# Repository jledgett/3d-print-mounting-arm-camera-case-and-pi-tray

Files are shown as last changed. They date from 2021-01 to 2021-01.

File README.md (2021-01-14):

# 3D Printer: Mounting Arm and Case for Raspberry Pi HQ Camera and Raspberry Pi / OctoPi

## Overview

This collection of files will allow you to 3D print a modification to your 3D printer.  This modification adds a mounting arm, case for the Raspberry Pi HQ Camera, as well as a covered tray for a Raspberry Pi 4B.  This is particularly useful for adding a camera to your printer for monitoring and control using OctoPrint / OctoPi.

This system was designed to work with the Creality CR-6 SE printer, but should work with __any__ printer or CNC that uses a 40mm x 40mm extruded aluminum frame (including Ender 3, Ender 3 Pro, CR-10 MAX) .

The Raspberry Pi case for your OctoPi server is designed to allow either direct mounting of the Raspberry Pi to the case using standoffs or dropping in the popular aluminum Flirc case for better heat dissipation.   

The case also supports mounting a **5v** 40mm fan.   Noctua fans are suggested due to their quiet operation and lengthy warranty.   They also included the 3-pin to 2-pin adapter which will allow you connect it directly to pins 4 and 6 of your Raspberry Pi's GPIO.

If you are using the Flirc case, the camera cable and fan cable can both be passed through the GPIO slot on the bottom of the Flirc case.   Remove the cosmetic black plastic TOP panel to increase cooling performance.

## Getting Started

You will need the following non-included parts:
- [Raspberry Pi 4B](https://smile.amazon.com/gp/product/B08DJ9MLHV/)
- [Raspberry Pi HQ Camera](https://www.canakit.com/raspberry-pi-hq-camera.html)
- [SD Card](https://smile.amazon.com/gp/product/B07FCMKK5X)
- [6mm CS-mount Lens](https://smile.amazon.com/gp/product/B088GWZPL1)
- [Flex Cable for Raspberry Pi Camera or Display - 18" / 457mm](https://www.adafruit.com/product/1730)
- [Mini Ball Head](https://smile.amazon.com/gp/product/B01N7RYA87) NOTE: Alternatively, you can mount directly to the mounting arm but will lose the ability to adjust the pitch of the camera up and down.
- [Noctua 40mm 5V Fan (3-pin)](https://smile.amazon.com/gp/product/B00NEMGCIA) (includes 3-pin to 2-pin adapter)
- *Screws, Nuts, Bolts*
  - (2x) 1/4"-20 x 1/2" bolts
  - (1x) 1/4"-20 jam nut
  - (4x) M4 x 40mm machine screws
  - (4x) M4 nuts
  - (6x) M4 washers
  - (4x) M2.5 x 30mm (or M2.5 x 35mm) 
  - (8x) M2.5 nuts
  - (8x) M2.5 washers
  - (4x) M2.5 nylon/rubber isolating washers
- [Flirc Raspberry Pi 4 Case](https://www.amazon.com/Flirc-Raspberry-Pi-Case-Silver/dp/B07WG4DW52/) _**OR**_
   - (4x) M2.5 x 10mm stand offs with matching screws
   - (4x) M2.5 nuts
   - (4x) M2.5 nylon/rubber isolating washers

You will need the following additional tools:
- Screwdriver for M2.5 screws
- Screwdriver for M4 screws
- Needle-nose pliers
- 1/4"-20 tap and die set for cleaning up threads of leveling feet

## Printing Instructions

:warning: **IMPORTANT:** Please review each part in your slicing software before printing to ensure a logical face is touching the build plate!      

These print settings were used to print using a Creality CR-6 SE using Hatchbox Black 1.75mm PLA.   You may need to adjust these settings slightly for other printer and filament combinations.

- Print Resolution: 0.2
- Infill (unless otherwise noted below): 40%
- Supports (unless otherwise noted below): No
- Printing Temperature: 200C
- Build Plate Temperature: 60C
- Part-specific notes:
   - **Short Leveling Foot 1g - Print 5.stl**: Print 5 of these at 100% infill.
   - **Long Leveling Foot 1g - Print 2.stl**: Print 2 of these at 100% infill.
   - **Tripod Thread Mount 34g.stl**: This piece is optional.   Print it if you want to mount accessories such as an LED light.   For this piece you will need to print a "Touching Buildplate" support for overhanging angles exceeding 47°.  This is the only piece that needs to be printed with supports.
  - **OPTIONAL Octopi Tray Spring Clip For FLIRC Case 4g.stl**: This is only needed if you are dropping in a Flirc case.  It ensures the case stays aligned properly.

## Assembly Instructions

1. Clean up the threaded parts (both male and female) using a tap and die.   Silicone spray can assist with lubricating the threads before screwing them.

1. Attach the fan to the OctoPi Tray using the self-tapping mounting screws that came with the fan.

1. Use an M4 screw and nut to attach the Mounting Arm to the Mounting Arm Rail Clamp.

1. Use the three remaining M4 screws, washers, and nuts as well as the OctoPi Tray spacers to attach the Mounting Arm to the OctoPi Tray. 

1. Attach the five Short Leveling Feet to the appropriate holes on the bottom of the OctoPi tray and Mounting Arm.

1. Snap the Mounting Arm Rail Clamp to the left front of the 3d printer.   

1. Attach the Raspberry Pi camera cable to the Raspberry Pi.

1. Attach the fan cable adapter to pins 4 and 6 (pin 4 is 5v, pin 6 is ground) of the Raspberry Pi.  

1. If using a Flirc case, unclip the cosmetic black top panel and set aside.  Place the Pi inside the case and route the cables through the bottom GPIO slot.

1. Place the Raspberry Pi in the OctoPi tray and route the Raspberry Pi camera cable through the triangular opening of the tray.   Feed the cable up through the cable guiding slot in the mounting arm.

1. Attach the lens to the camera.

1. Feed the other end of the Raspberry Pi camera cable through the slot of the Camera Case back and attach it to the Raspberry Pi HQ Camera.  Ensure correct orientation.  

1. Place the four M2.5 x 30mm screws and washers through the rear of the Camera case back and the HQ camera.   Place a nylon/rubber M2.5 washer on each of the four screws.   Then place an M2.5 nut on each of the four screws, finger tightening to hold the camera in place.  

1. Attach the mini ball head to the Mounting Arm using 1/4"-20 x 1/2" bolt.

1. Screw the 1/4"-20 jam nut on the mini ball head.    

1. Carefully attach the Camera case back and HQ camera to the mini ball head using the HQ camera's integrated tripod thread.   Tighten the jam nut in place to secure the the camera.

1. Route the USB-C power source along the rail of your printer, tucking the cord into the top channel of the aluminum extrusion where possible.   Route the cable under the OctoPi Tray spacer closest to the printer.

1. Route the USB-C power source through the square hole in the OctoPi Tray Lid and plug it in to the Raspberry Pi.   

1. If using a Flirc case, place the spring clip in the side of the case closest to the USB and network ports.   This clip simply holds the Flirc case against the side of the case opposite the fan.

1. Drop the OctoPi Tray Lid in place.

1. Use the USB C cord retainers to clip the USB C power source into place on the rail.

1. [Install OctoPi on your Raspberry Pi](https://octoprint.org/download/) (the SD card is accessible through the slot on the end of the OctoPi Tray).

1. Once OctoPi is running, go the Control tab and you should see a web camera image.    

1. The camera may appear in 4:3 ratio instead of 16x9 regardless of the OctoPrint settings.   You can fix this by SSHing into your OctoPi and editing: `boot/octopi.txt`

1. Adjust the focus and apeture of your camera and tighten the adjustment thumbscrews in place.   

1. Slide the Camera Case Front carefully on to the four screws.   Using the M2.5 washers and nuts, carefully secure the case in place.

1. If you wish to use the Tripod Thread Mount, insert the 2 Long Leveling Feet to the mount.

1. Clamp the Tripod Thread Mount to the left rear of the 3d printer.   Your light, etc. can be attached to the mount using the remaining 1/4"-20 x 1/2" bolt.

1. Adjust all the leveling feet.

1. Plug in a voltage isolated **(NO 5V PIN!)** USB-A to Micro USB cable from the Raspberry Pi to the printer.  It is **very important** to ensure that your cable does not have a 5V pin or your printer  and Raspberry Pi may be damaged!

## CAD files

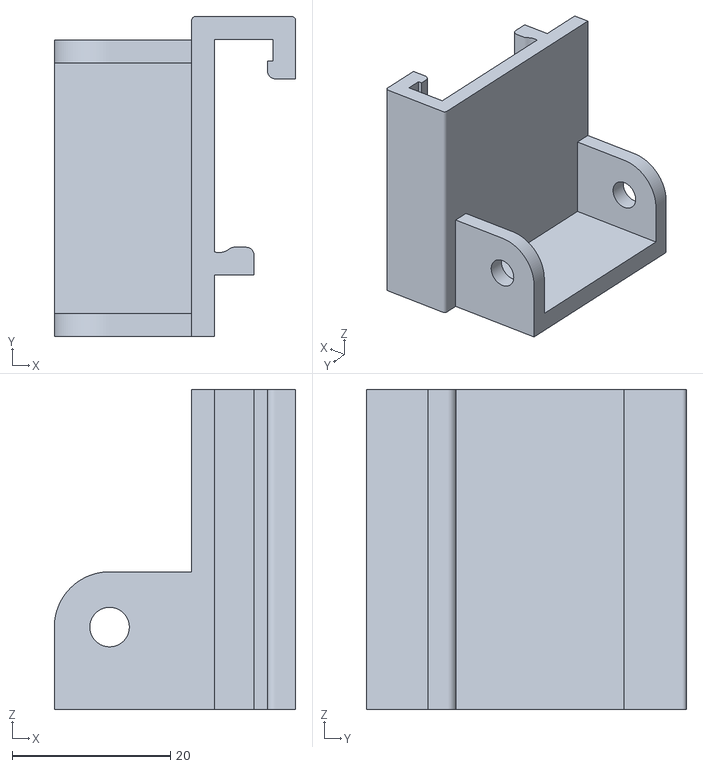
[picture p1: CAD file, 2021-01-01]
Mounting Arm Rail Clamp 10g.stl
30.6 x 40.5 x 40.5

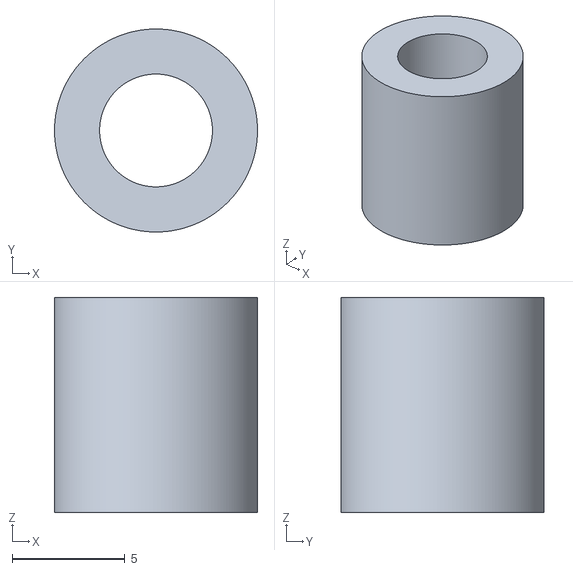
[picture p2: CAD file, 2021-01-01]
Octopi Tray Spacer 1g - Print 3.stl
9.00 x 9.00 x 9.55

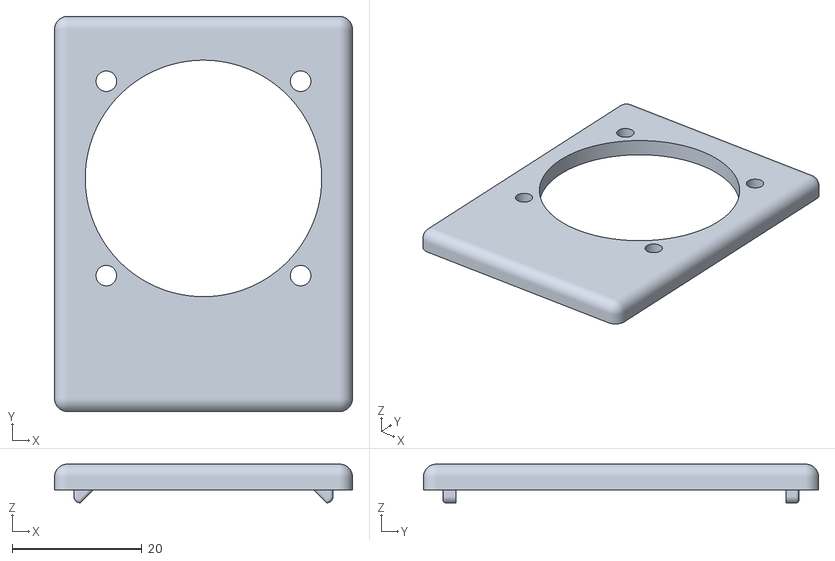
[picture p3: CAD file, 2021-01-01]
Camera Case Front 6g.stl
46.0 x 61.0 x 6.00

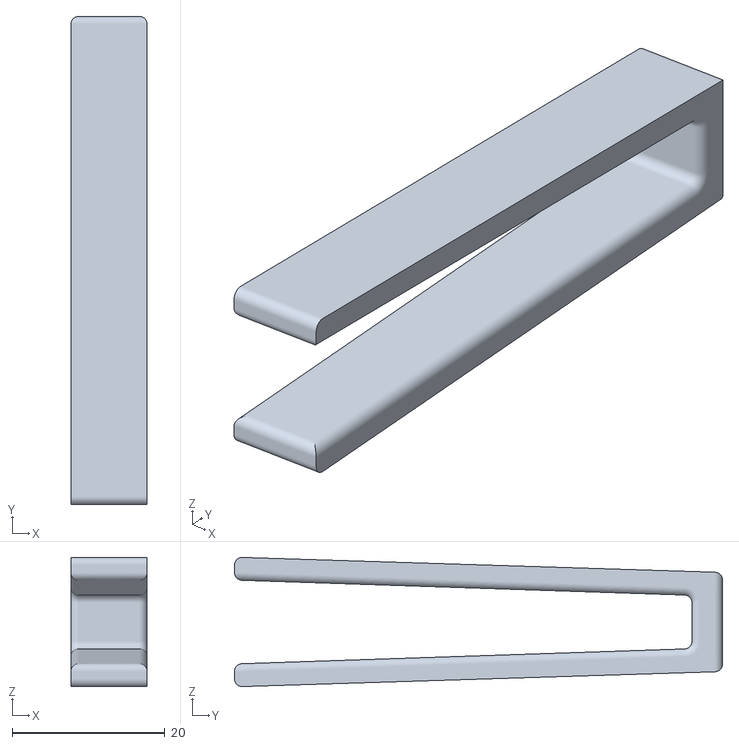
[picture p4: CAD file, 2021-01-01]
OPTIONAL Octopi Tray Spring Clip For FLIRC Case 4g.stl
10.0 x 64.0 x 16.9

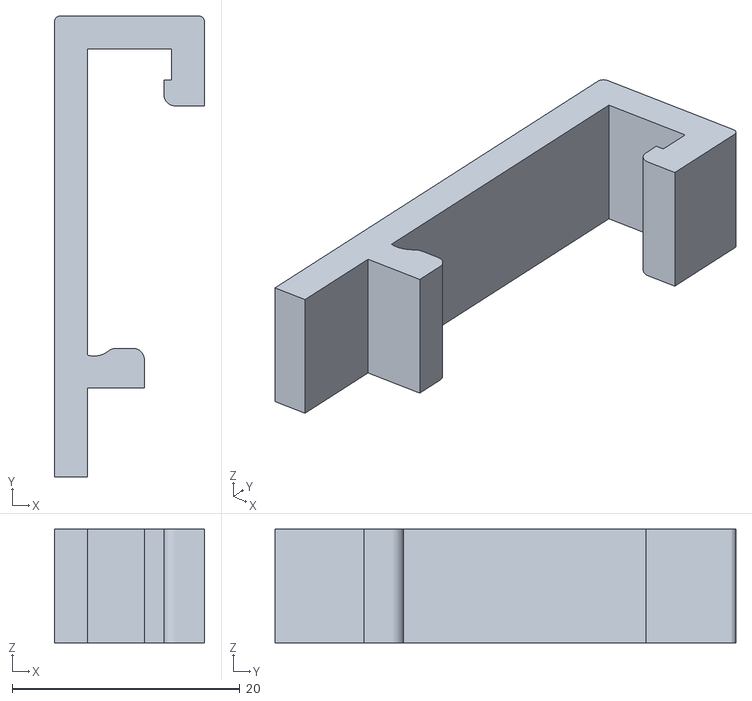
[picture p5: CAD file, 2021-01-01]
USB C Cord Retainer 2g - Print 2.stl
13.2 x 40.5 x 10.0

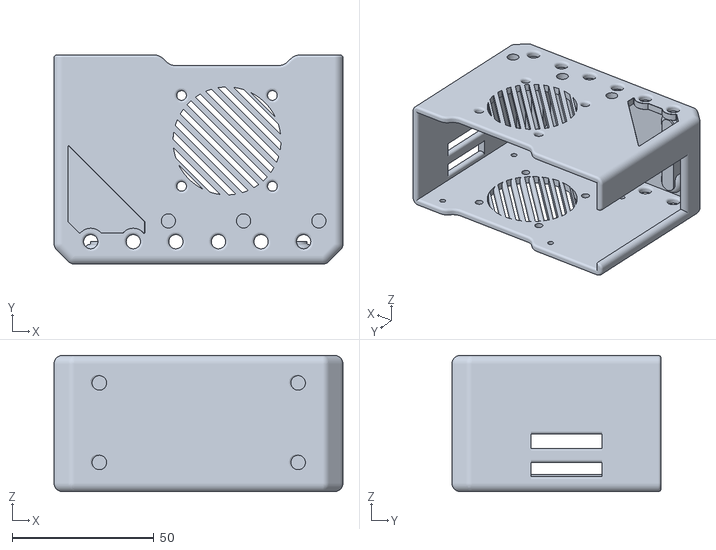
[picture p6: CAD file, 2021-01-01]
Octopi Tray 60g.stl
101.8 x 73.7 x 48.0

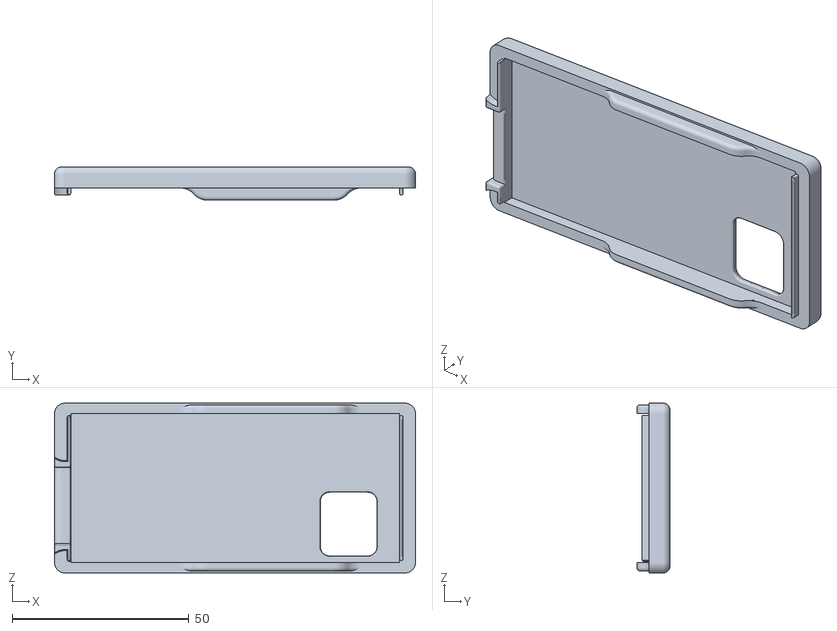
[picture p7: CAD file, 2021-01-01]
Octopi Tray Lid 16g.stl
102.0 x 9.41 x 48.0

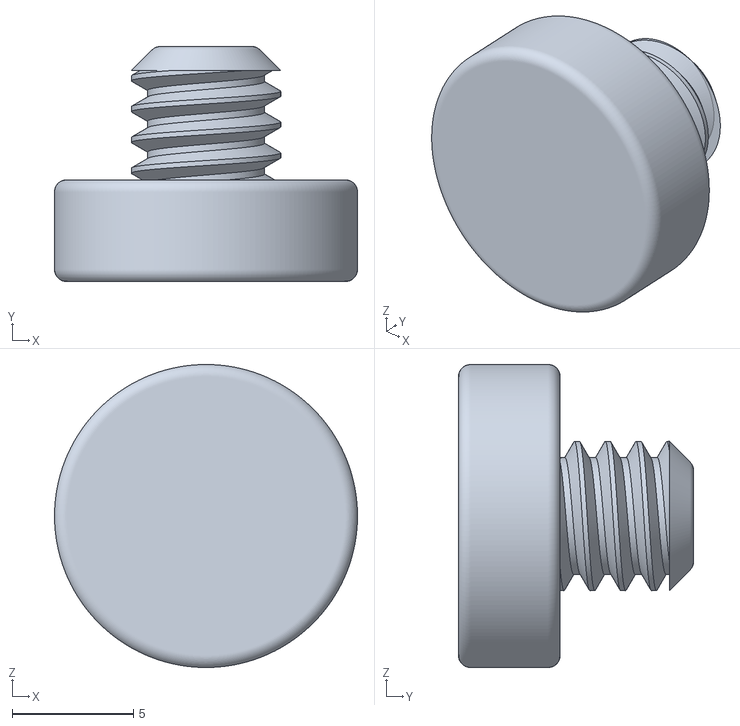
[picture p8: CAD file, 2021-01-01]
Short Leveling Foot 1g - Print 5.stl
12.5 x 9.70 x 12.5

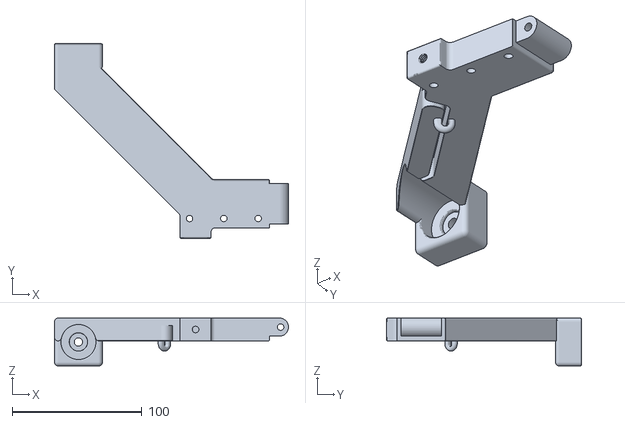
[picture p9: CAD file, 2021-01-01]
Mounting Arm 92g.stl
180.6 x 150.3 x 37.0

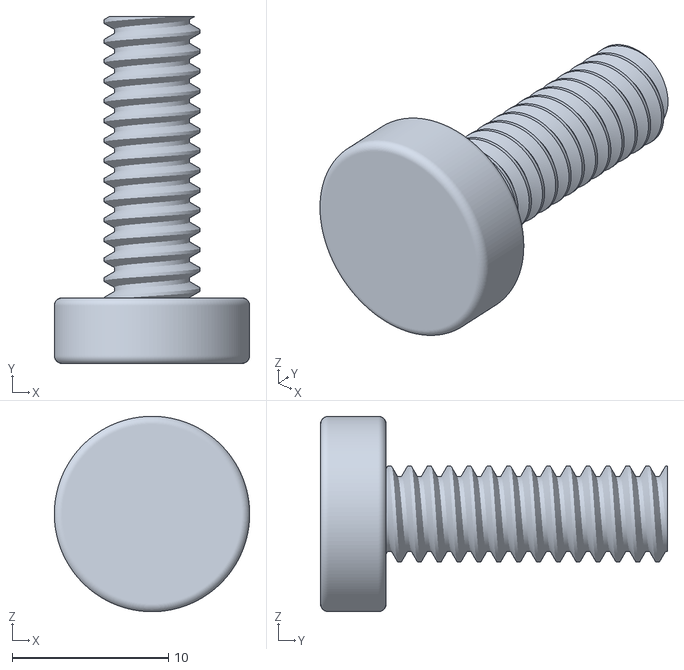
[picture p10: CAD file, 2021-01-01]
Long Leveling Foot 1g - Print 2.stl
12.5 x 22.2 x 12.5

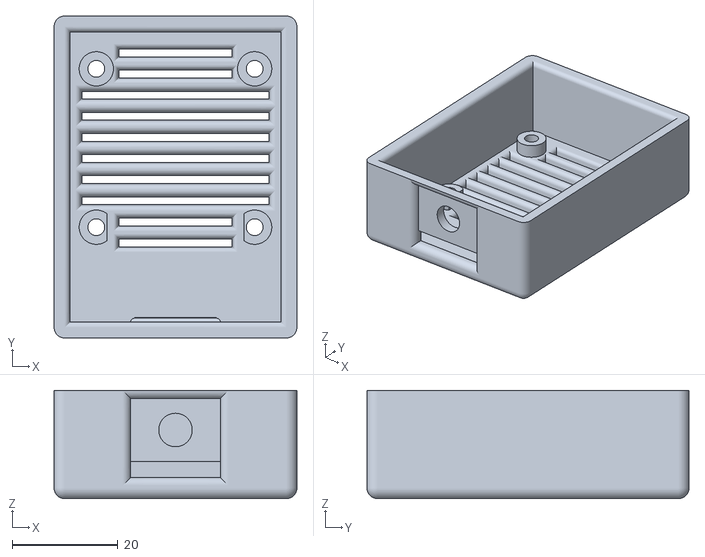
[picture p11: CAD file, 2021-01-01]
Camera Case Back 17g.stl
46.0 x 61.0 x 20.5

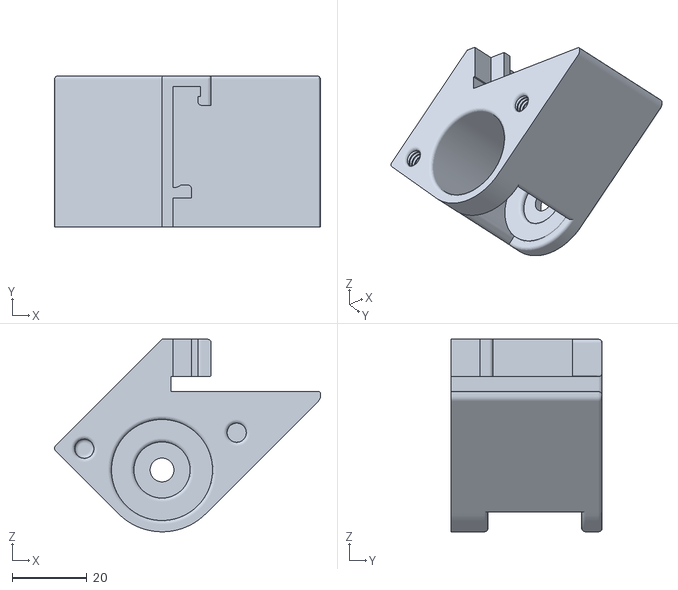
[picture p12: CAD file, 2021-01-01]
Tripod Thread Mount 34g.stl
71.1 x 40.5 x 51.5
